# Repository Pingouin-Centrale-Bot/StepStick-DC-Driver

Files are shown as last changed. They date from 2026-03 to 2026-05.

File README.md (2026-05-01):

# StepStick DC Driver V2
A dual DC/H-bridge driver, designed as a drop-in replacement for a standard stepstick.  
Can drive two DC motors, or be used as four independent half-bridges.  
Designed around the `TB67H453FNG` IC. Datasheets can be found [here](Components/TB67H453FNG/).

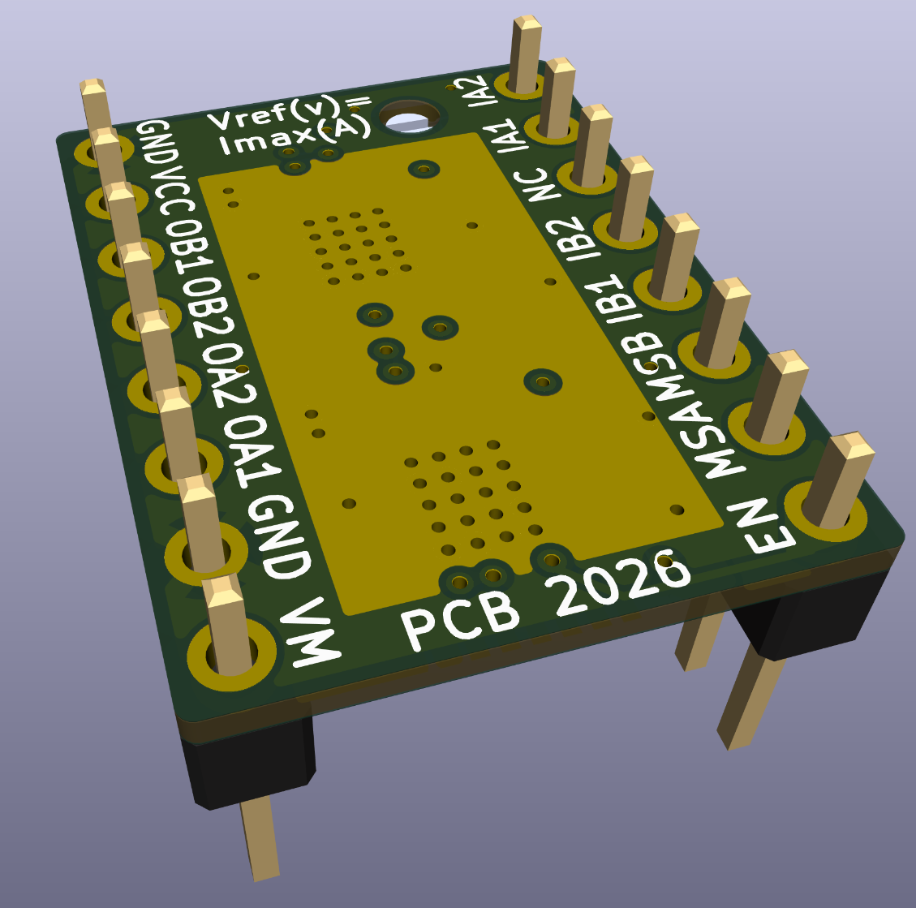
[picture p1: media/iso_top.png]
iso top view

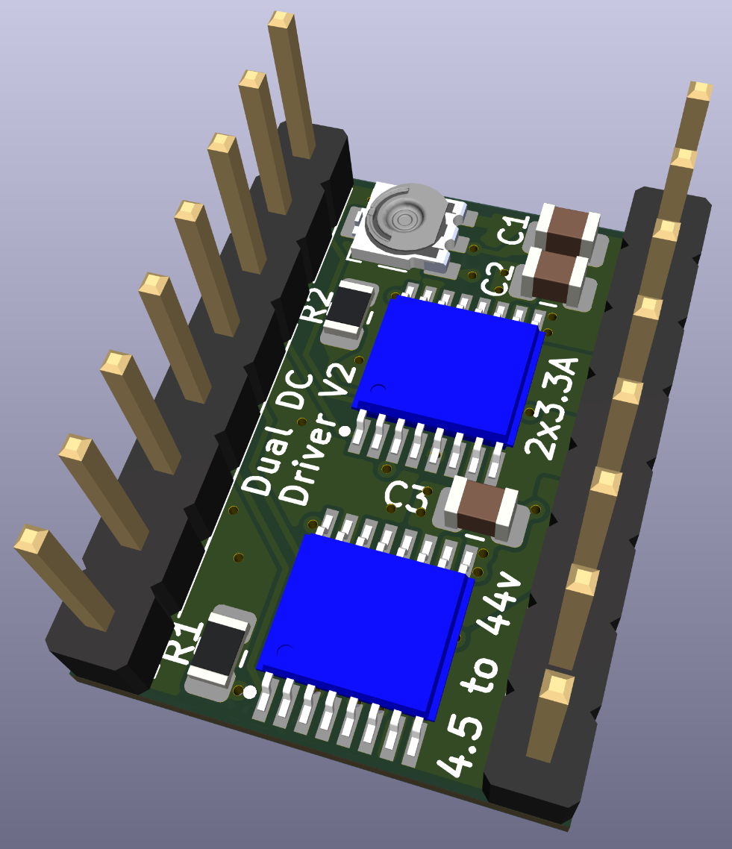
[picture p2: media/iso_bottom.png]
iso bottom view


## Specs
- Dual H-Bridge : Can drive two DC loads in both directions, or four DC loads unidirectionally
- 3.3A Max per channel
- Accepts an input power voltage from 4.5v to 44v
- Based around a 4 layer PCB, to improve heat dissipation (a heat sink and active cooling is highly recommended)
- The maximum intensity can be configured with the trimmer, by adjusting Vref
- Can be enabled or disabled with the `en` pin, just like a standard stepstick
- Compatible with both 5v and 3.3v logic voltage (If using 5v to power VCC, you must adjust the trimmer so that Vref stays below 3.3v!)

## Pinout
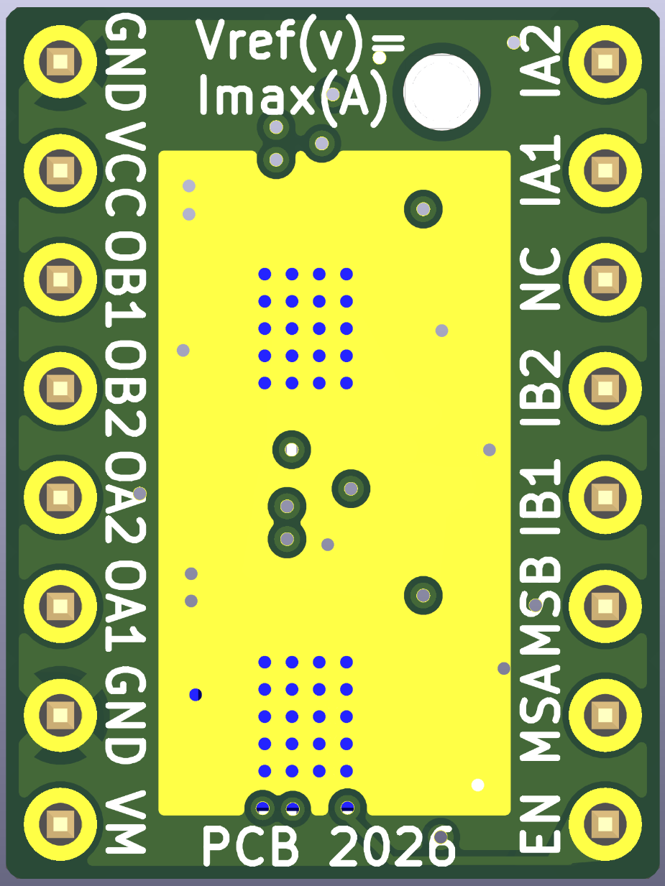
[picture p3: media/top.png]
pinout


You can use the `Pololu_Breakout_A4988` symbol from the default KiCad library, with its accompanying default footprint. Here is a pinout correspondence for the pins :

| StepStick DC Driver | Pololu A4988 |
|:---:|:---:|
| OB1 | 1B |
| OB2 | 1A |
| OA2 | 2A |
| OA1 | 2B |
| IA2 | DIR |
| IA1 | STEP |
| IB2 | RESET |
| IB1 | MS3 |
| MSB | MS2 |
| MSA | MS1 |
| VCC | VDD |
| NC | SLEEP |

> [!WARNING]
> You need to add a 100uf capacitor between the `VM` and `GND` pins.

## Configuration
If the resistors on the BOM are respected, the maximum intensity per channel can be configured by setting the `Vref` voltage :  
Imax(A)=Vref(v)
The driver will regulate the intensity to prevent it from getting higher.

The configuration is common to both H-bridge.

## Control
Channel A and B are both controlled by their own two pins `Ix1` and `Ix2`.  
They are 3 ways to control the outputs, configured respectively by `MSx` :

| MSx | Mode |
|:---:|:---:|
|  L  | Phase/Enable control |
|  H  |  PWM control |
| Hi-z/Open| Individual half bridge control |

### Phase/Enable control (MSx=Low)

| Ix1 | Ix2 | Ox1 | Ox2 | Mode |
|:---:|:---:|:---:|:---:|:---:|
|  L  | L/H |  L  |  L  | Short Brake |
|  H  |  L  |  L  |  H  | Reverse |
|  H  |  H  |  H  |  L  | Forward |

### PWM control (MSx=High)

| Ix1 | Ix2 | Ox1 | Ox2 | Mode |
|:---:|:---:|:---:|:---:|:---:|
|  L  |  L  |  Hi-Z  |  Hi-Z  | Coast |
|  L  |  H  |  L  |  H  | Reverse |
|  H  |  L  |  H  |  L  | Forward |
|  H  |  H  |  L  |  L  | Short brake |

### Individual half bridge control (MSx=Hi-z/Open)

| Ixx | Oxx | Mode |
|:---:|:---:|:---:|
|  L  |  L  | Short Brake |
|  H  |  H  | Reverse |

> [!NOTE]
> Current limiting does not work in half bridge mode, so beware of currents!

### All

If left open, a pin will be pulled down (considered L).
If you do not want to use one of the channels, you can simply not connect the output to anything.

## Fabrication notes
The constraints have been set up for Aisler's Beautiful Boards service.  
It is advised to use a .8mm total thickness instead of the standard 1.6mm to improve the thermal dissipation.

## Real world testing
### Issues found
- Silkscreen is inverted between IAx and IBx
- The enable logic is reversed to what it should be if trying to emulate a stepstick

### Notes
When an overcurrent event happens, the driver deactivates for 25us. In the event of a short circuit, this means the driver will be off most of the time, and so the measured intensity (mean intensity) will be very low, and so the driver cannot be used to regulate current.

### Power dissipation
No overheating was found when used at .8A on one channel. Further testing is necessary.

# StepStick DC Driver V1
See [here](/V1/).

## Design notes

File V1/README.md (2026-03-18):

# StepStick DC Driver
A dual DC/H-bridge driver, designed as a drop-in replacement for a standard stepstick.  
Designed around the `TB67H481FNG` IC. Datasheets can be found [here](Components/TB67H481FNG/).

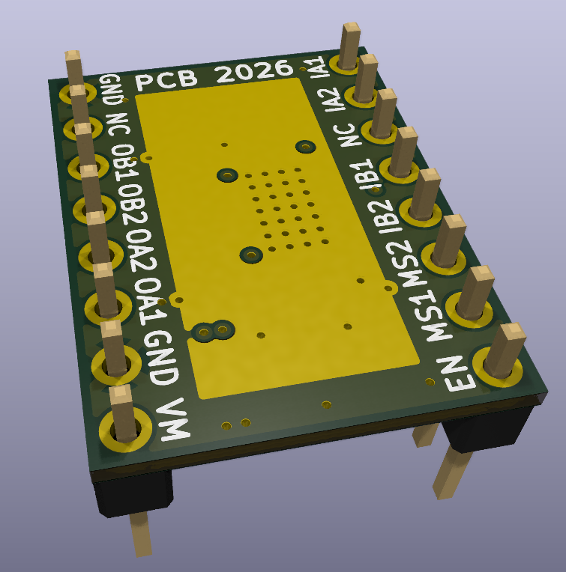
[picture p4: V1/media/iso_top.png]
iso top view

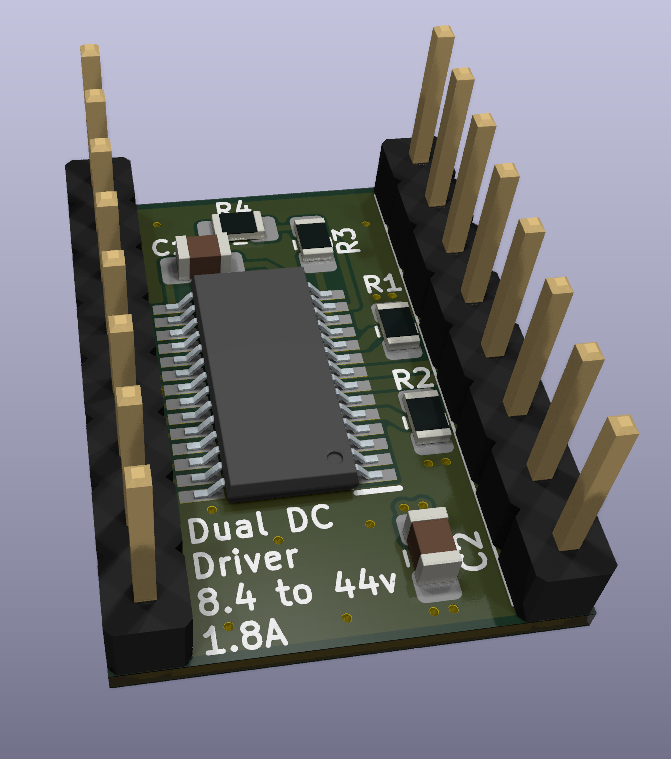
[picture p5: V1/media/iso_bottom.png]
iso bottom view


## Specs
- Dual H-Bridge : Can drive two DC loads in both directions
- 1.8A Max per channel
- Accepts an input power voltage between 8.4 and 44v
- Based around a 4 layer PCB, to improve heat dissipation (a heat sink and active cooling is highly recommended)
- A maximum intensity can be configured with the `MS1` and `MS2` pins
- Can be enabled or disabled with the `en` pin, just like a standard stepstick
- Compatible with both 5v and 3.3v logic voltage

## Pinout
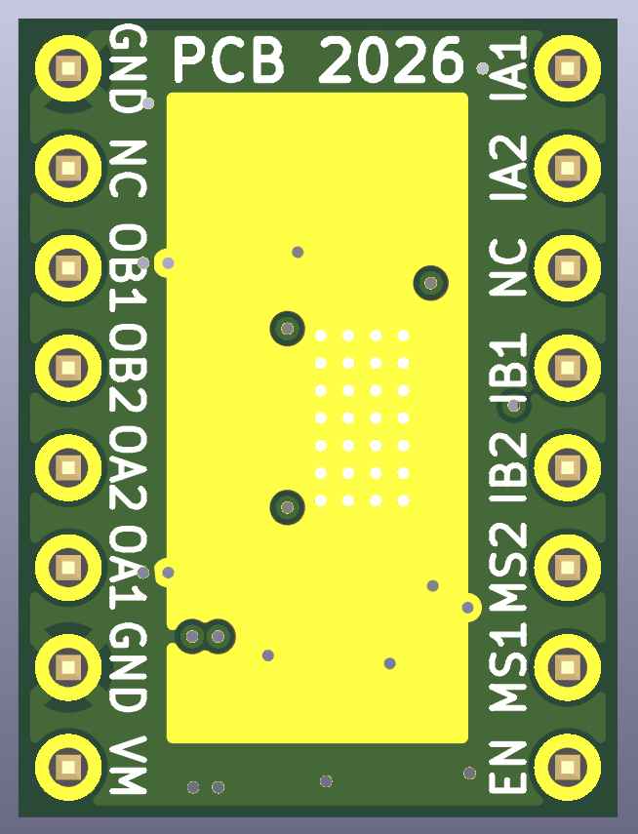
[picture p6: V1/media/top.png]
pinout


You can use the `Pololu_Breakout_A4988` symbol from the default KiCad library, with its accompanying default footprint. Here is a pinout correspondence for the pins :

| StepStick DC Driver | Pololu A4988 |
|:---:|:---:|
| OB1 | 1B |
| OB2 | 1A |
| OA2 | 2A |
| OA1 | 2B |
| IA1 | DIR |
| IA2 | STEP |
| IB1 | RESET |
| IB2 | MS3 |
| NC |  VDD, SLEEP  |

> [!WARNING]
> You need to add a 100uf capacitor between the `VM` and `GND` pins.

## Configuration
If the resistors on the BOM are respected, the maximum intensity per channel can be configured with the `MS1` and `MS2` pins :

| MS1 | MS2 | Torque | Max current per channel |
|:---:|:---:|:---:|:---:|
|  L  |  L  | 100% | 1.8A |
|  L  |  H  | 71% | 1.3A |
|  H  |  L  | 38% | .7A |
|  H  |  H  | 0% (Output OFF) | 0A |

If left open, a pin will be pulled down (considered L).
The configuration is the same for both channels.  

## Control
Channel A and B are both controlled by their own two pins Ix1 and Ix2 :

| Ix1 | Ix2 | Ox1 | Ox2 | Mode |
|:---:|:---:|:---:|:---:|:---:|
|  L  |  L  |  L  |  L  | Short Brake |
|  L  |  H  |  L  |  H  | Counterclockwise |
|  H  |  L  |  H  |  L  | Clockwise |
|  H  |  H  |  H  |  H  | Short brake |

If left open, a pin will be pulled down (considered L).
If you do not want to use one of the channels, you can simply not connect the output to anything.

## Fabrication notes
The constraints have been set up for Aisler's Beautiful Boards service.  
It is advised to use a .8mm total thickness instead of the standard 1.6mm to improve the thermal dissipation.

## Real world testing
To be done.

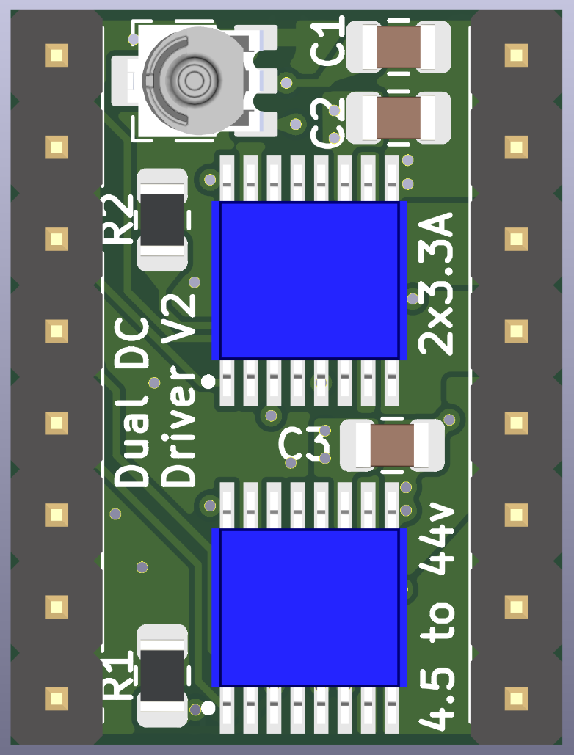
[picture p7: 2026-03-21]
media/bottom.png

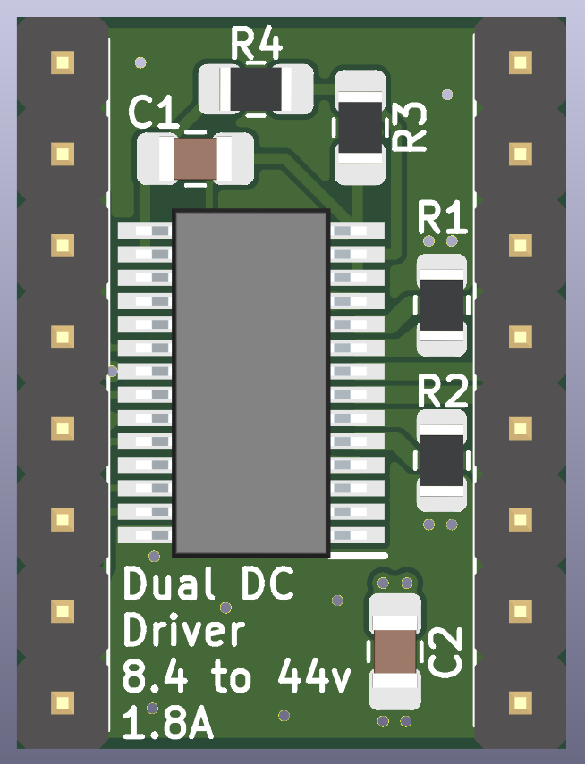
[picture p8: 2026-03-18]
V1/media/bottom.png

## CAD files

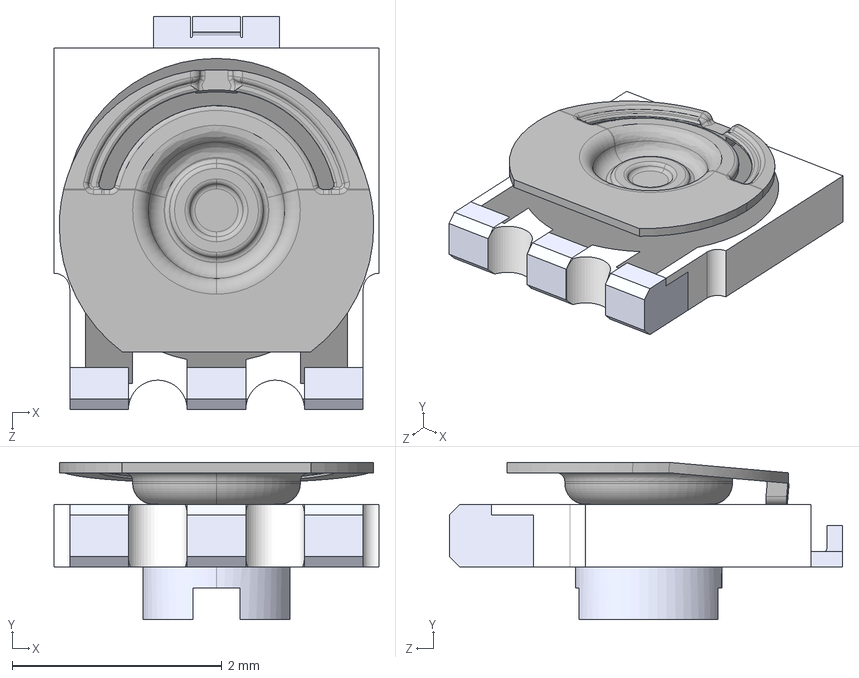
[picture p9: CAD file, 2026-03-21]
Components/POT_EVM3R/EVM-3RSX50B14.STEP
3.10 x 1.50 x 3.75 mm

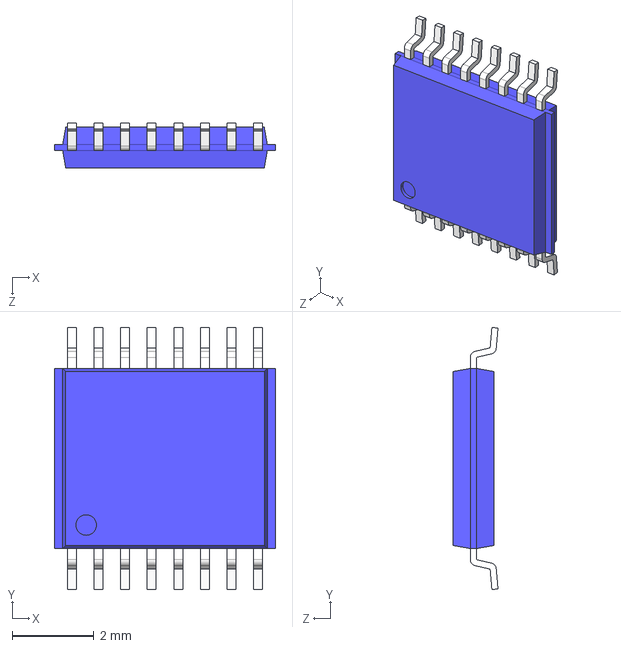
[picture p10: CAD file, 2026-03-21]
Components/TB67H453FNG/TSSOP16.STEP
5.40 x 6.40 x 1.10 mm

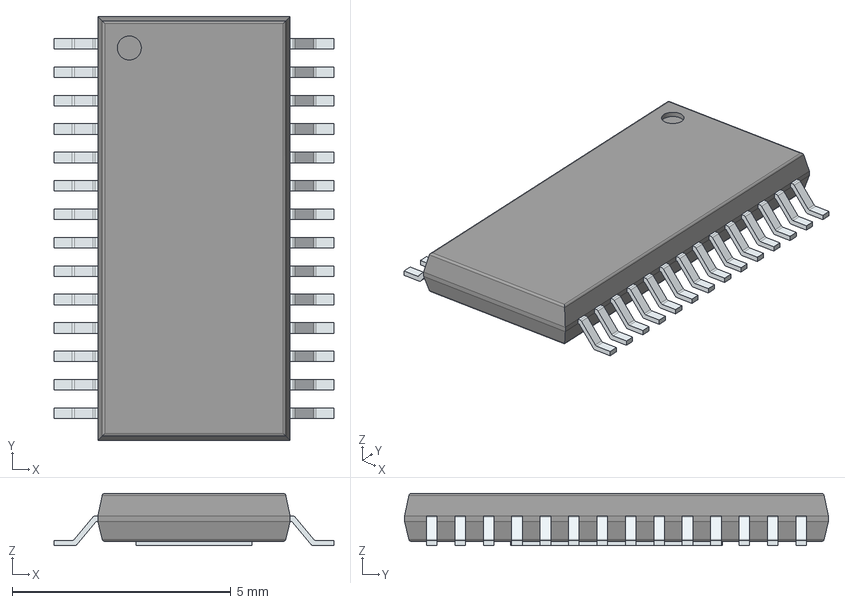
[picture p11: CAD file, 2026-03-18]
V1/Components/TB67H481FNG/TB67H481FNG.stp
6.40 x 9.70 x 1.20 mm
PinsArrayLR
ThermalPad

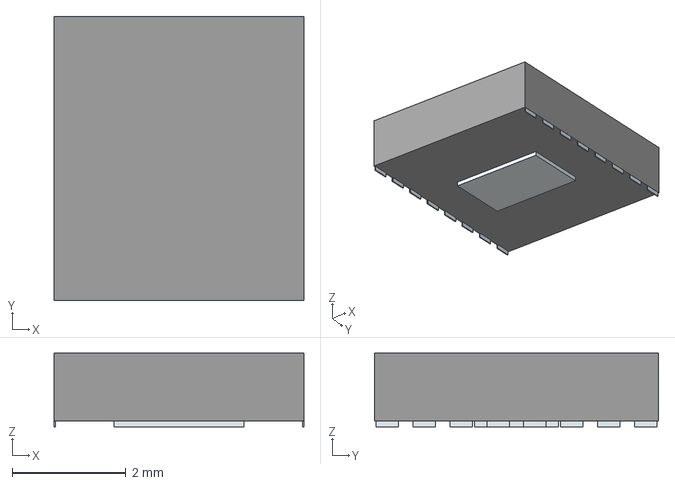
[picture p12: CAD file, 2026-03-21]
Components/TB67H453FNG/TB67H453FNG.stp
4.40 x 5.00 x 1.30 mm
Pins

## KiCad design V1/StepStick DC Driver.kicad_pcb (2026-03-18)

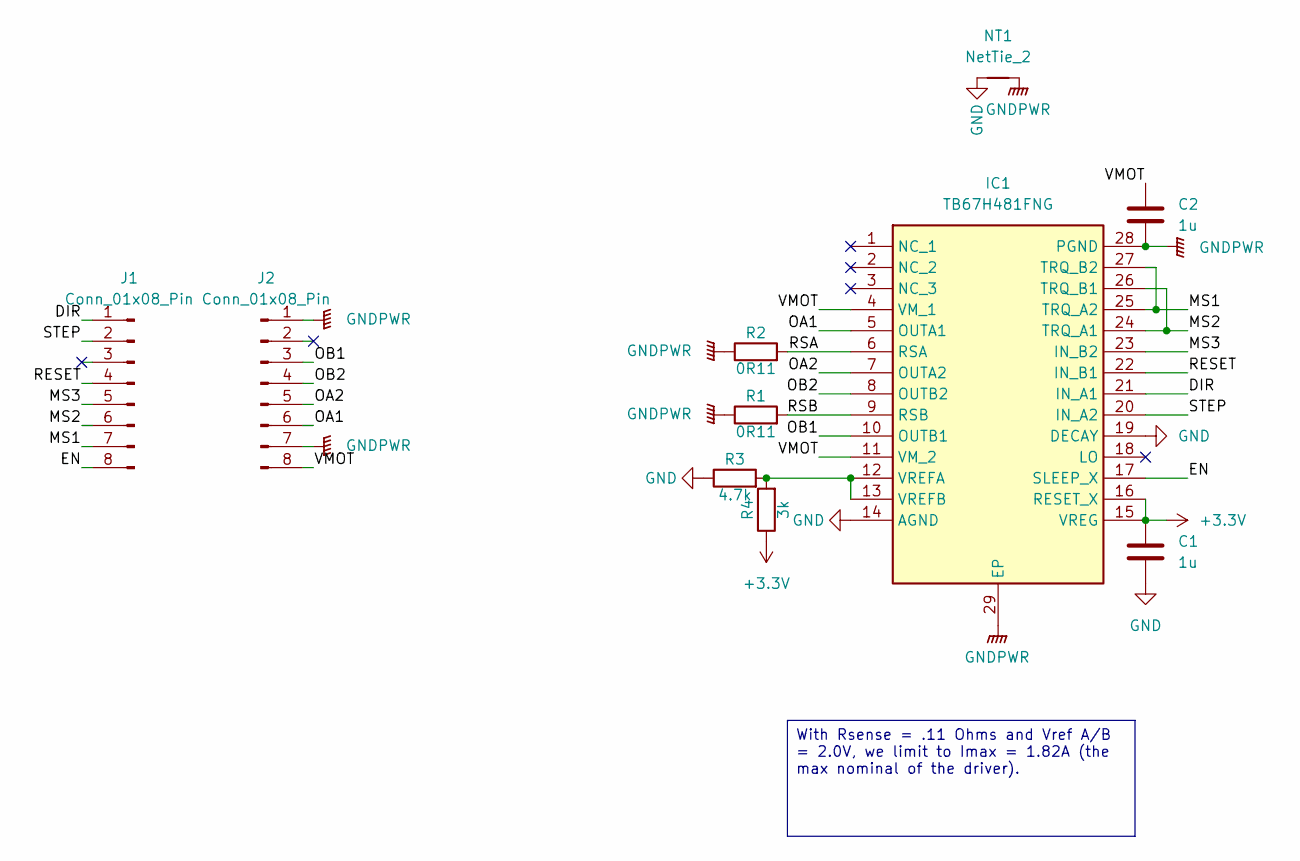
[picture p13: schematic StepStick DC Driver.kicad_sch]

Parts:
C1, C2: 1u; C_0805_2012Metric_Pad1.18x1.45mm_HandSolder
IC1: TB67H481FNG; SOP65P640X120-29N; Manufacturer_Part_Number TB67H481FNG
J1, J2: Conn_01x08_Pin; PinHeader_1x08_P2.54mm_Vertical
NT1: NetTie_2; NetTie-2_SMD_Pad0.5mm
R1, R2: 0R11; R_0805_2012Metric
R3: 4.7k; R_0805_2012Metric_Pad1.20x1.40mm_HandSolder
R4: 3k; R_0805_2012Metric_Pad1.20x1.40mm_HandSolder

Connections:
+3.3V: C1.1, IC1.15 (VREG), IC1.16 (RESET_X), R4.1
/DIR: IC1.21 (IN_A1), J1.1
/EN: IC1.17 (SLEEP_X), J1.8
/MS1: IC1.25 (TRQ_A2), IC1.27 (TRQ_B2), J1.7
/MS2: IC1.24 (TRQ_A1), IC1.26 (TRQ_B1), J1.6
/MS3: IC1.23 (IN_B2), J1.5
/OA1: IC1.5 (OUTA1), J2.6
/OA2: IC1.7 (OUTA2), J2.5
/OB1: IC1.10 (OUTB1), J2.3
/OB2: IC1.8 (OUTB2), J2.4
/RESET: IC1.22 (IN_B1), J1.4
/RSA: IC1.6 (RSA), R2.2
/RSB: IC1.9 (RSB), R1.2
/STEP: IC1.20 (IN_A2), J1.2
/VMOT: C2.1, IC1.4 (VM_1), IC1.11 (VM_2), J2.8
GND: C1.2, IC1.14 (AGND), IC1.19 (DECAY), NT1.1, R3.1
GNDPWR: C2.2, IC1.28 (PGND), IC1.29 (EP), J2.1, J2.7, NT1.2, R1.1, R2.1
unnamed: IC1.12 (VREFA), IC1.13 (VREFB), R3.2, R4.2

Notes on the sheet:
With Rsense = .11 Ohms and Vref A/B = 2.0V, we limit to Imax = 1.82A (the max nominal of the driver).

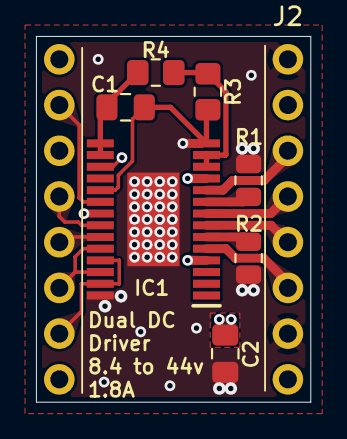
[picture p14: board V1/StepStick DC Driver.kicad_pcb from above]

Board: 4 copper layers, 15.2 x 20.3 mm, 10 parts (0 on the bottom side), 18 nets.

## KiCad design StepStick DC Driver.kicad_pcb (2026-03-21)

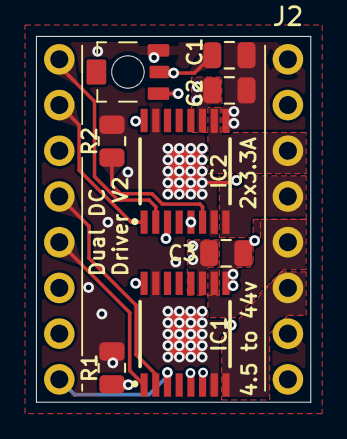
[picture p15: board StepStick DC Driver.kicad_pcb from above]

Board: 4 copper layers, 15.2 x 20.3 mm, 10 parts (0 on the bottom side), 17 nets.

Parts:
C1, C2, C3: 1u; C_0805_2012Metric
IC1, IC2: TB67H453FNG
J1, J2: Conn_01x08_Pin; PinHeader_1x08_P2.54mm_Vertical
R1, R2: 1k; R_0805_2012Metric
RV1: R_Potentiometer_Trim 100k; POT_EVM3R

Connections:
/DIR: IC2.2 (PH/IN2_), J1.1
/EN: IC1.3 (NSLEEP), IC2.3 (NSLEEP), J1.8
/MS1: IC1.16 (PMODE), J1.7
/MS2: IC2.16 (PMODE), J1.6
/MS3: IC1.1 (EN/IN1_), J1.5
/OA1: IC1.8 (OUT1), J2.6
/OA2: IC1.10 (OUT2), J2.5
/OB1: IC2.10 (OUT2), J2.3
/OB2: IC2.8 (OUT1), J2.4
/RESET: IC1.2 (PH/IN2_), J1.4
/STEP: IC2.1 (EN/IN1_), J1.2
/VCC: J2.2, RV1.1
/VMOT: C2.2, C3.2, IC1.11 (VM), IC2.11 (VM), J2.8
/VREF: C1.1, IC1.5 (VREF), IC2.5 (VREF), RV1.2
GND: C1.2, C2.1, C3.1, IC1.7 (IMODE), IC1.9 (PGND), IC1.15 (GND), IC1.17 (EP), IC2.7 (IMODE), IC2.9 (PGND), IC2.15 (GND), IC2.17 (EP), J2.1, J2.7, R1.1, R2.1, RV1.3
unnamed: IC1.6 (ISENSE), R1.2
unnamed: IC2.6 (ISENSE), R2.2
